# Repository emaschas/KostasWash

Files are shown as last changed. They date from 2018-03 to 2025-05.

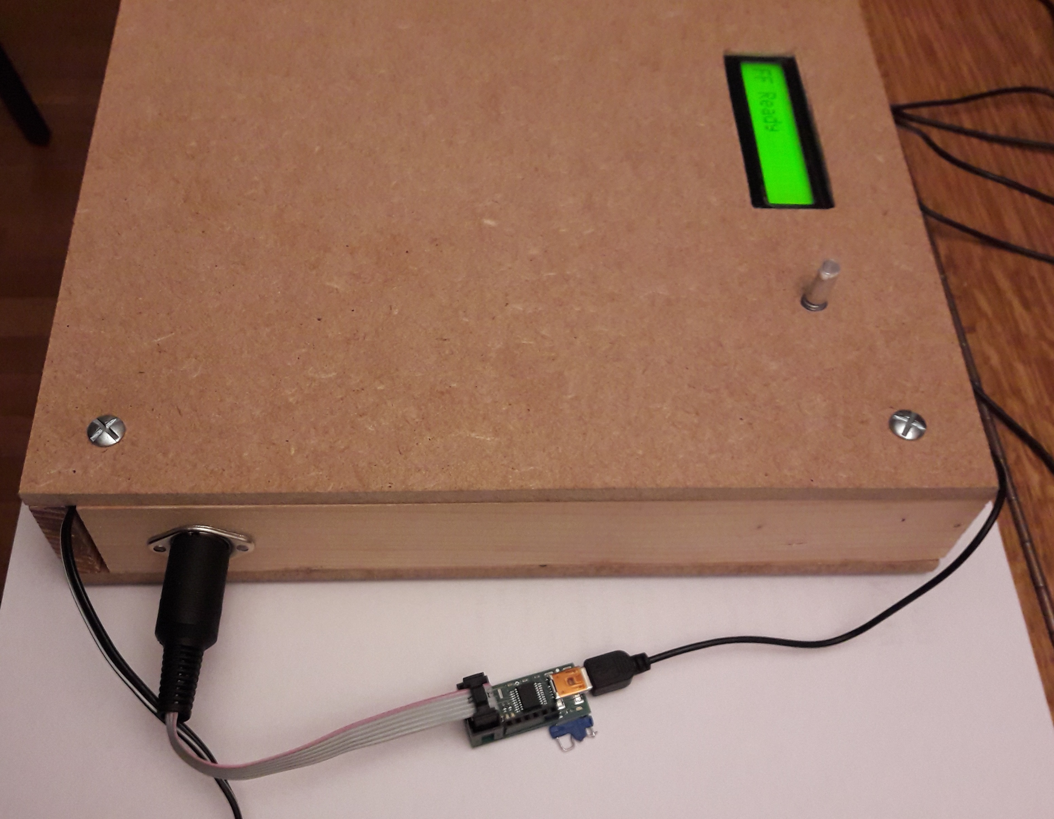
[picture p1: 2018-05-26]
Hardware/Controller_02.jpg

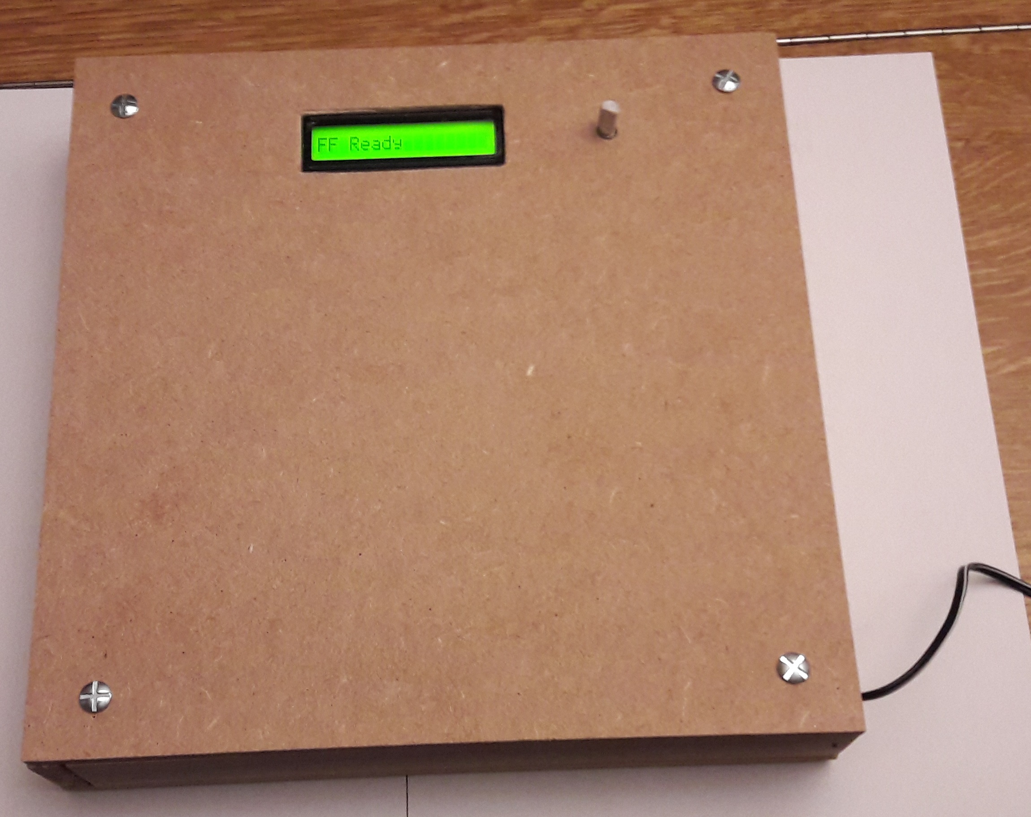
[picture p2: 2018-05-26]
Hardware/Controller_01.jpg

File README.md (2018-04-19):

# KostasWash
<h1>AVR based Washing machine controller</h1>
<h2>Object</h2>
This software is a washing machine controller based on an ATMEGA8535.
<h2>Human interface</h2>
The human interface is based on a LCD and a rotary encoder.
<h2>Power interface</h2>
The power interface is based on a 16 relay board.
<h2>Mechanical part</h2>
The washing machine is an old GROENJE WA583 with a broken mechanical programmer.<br>
The diagram and some other information can be found in the "Documentation" folder.
<h2>More details</h2>
See the <i>Wiki</i> pages for more details...

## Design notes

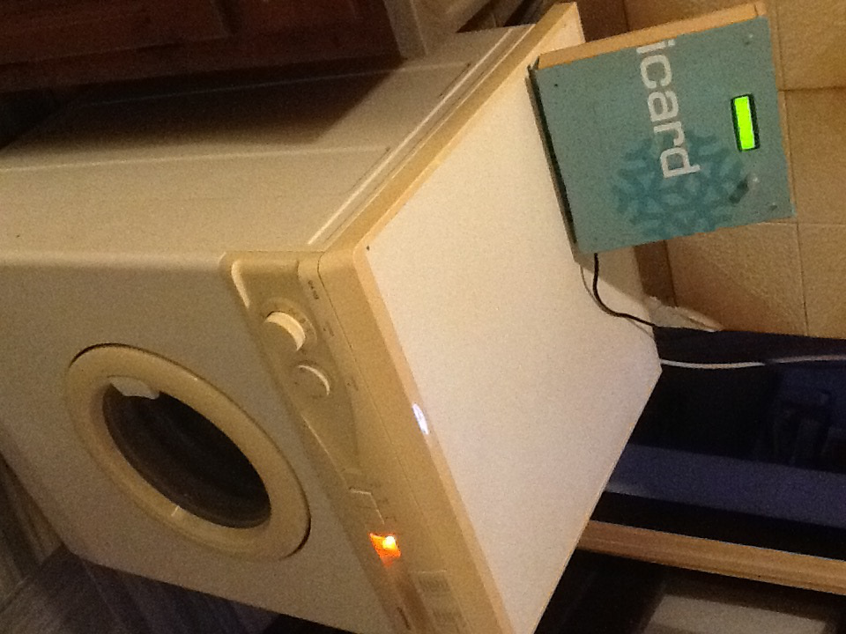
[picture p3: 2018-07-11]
Hardware/General_View.jpeg

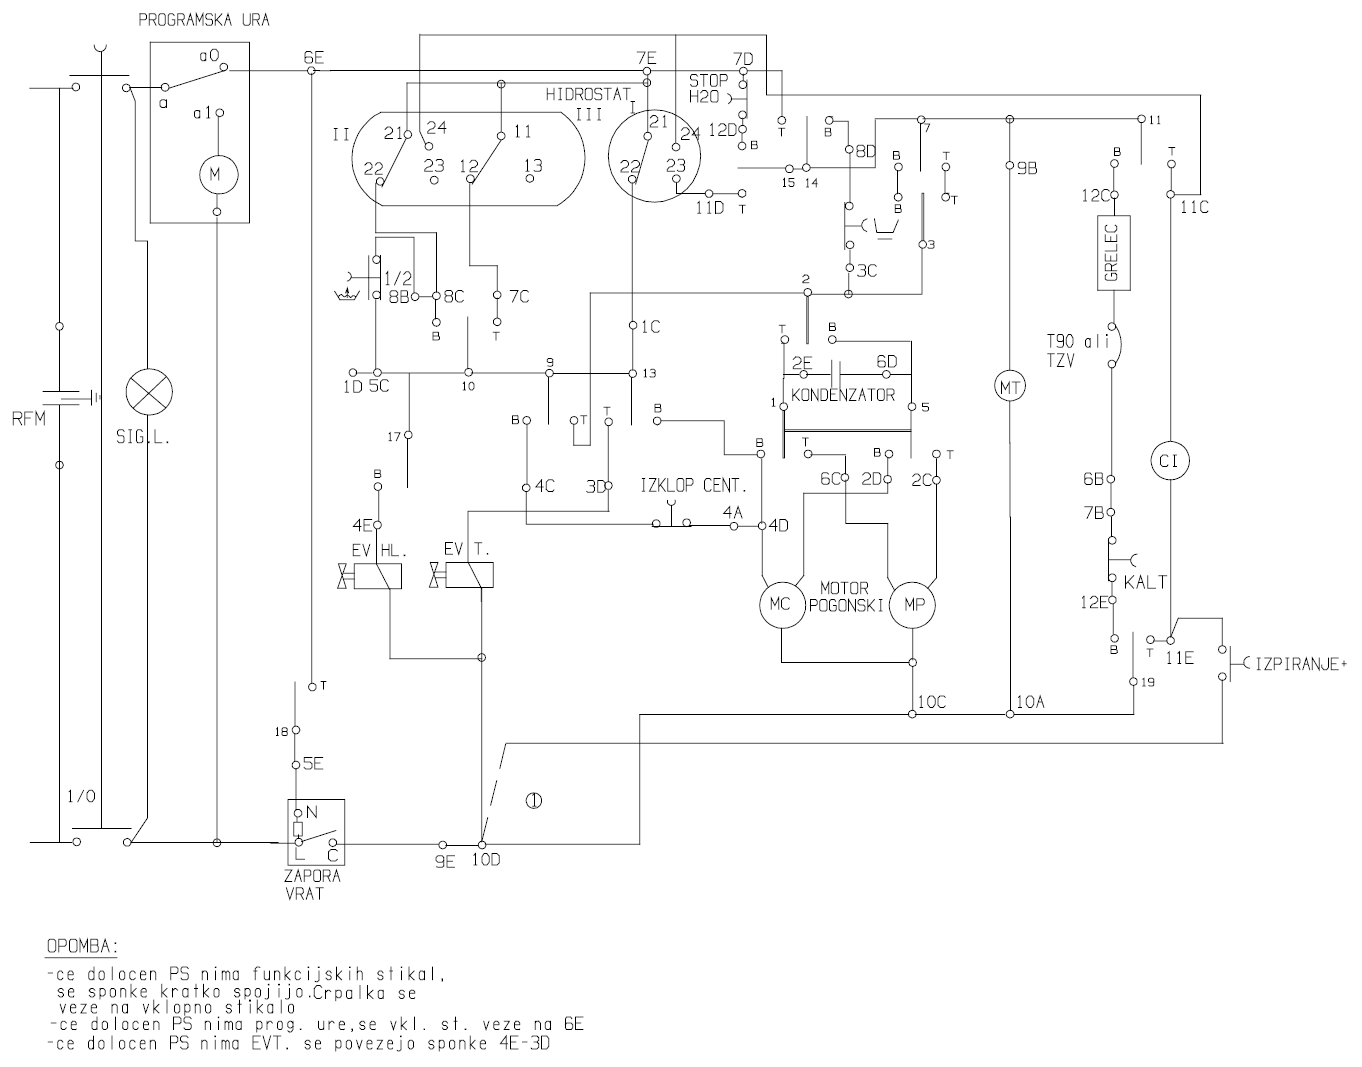
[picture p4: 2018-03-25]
Documentation/WA583 Diagram.png

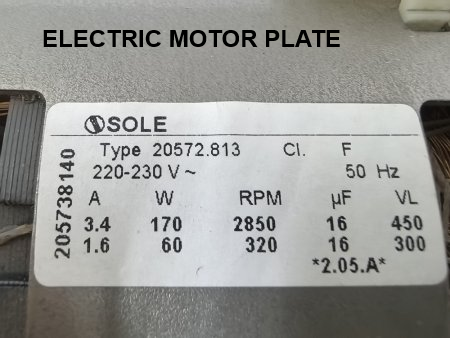
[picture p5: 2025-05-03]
Documentation/Gorenje WA583 Motor 606278.png

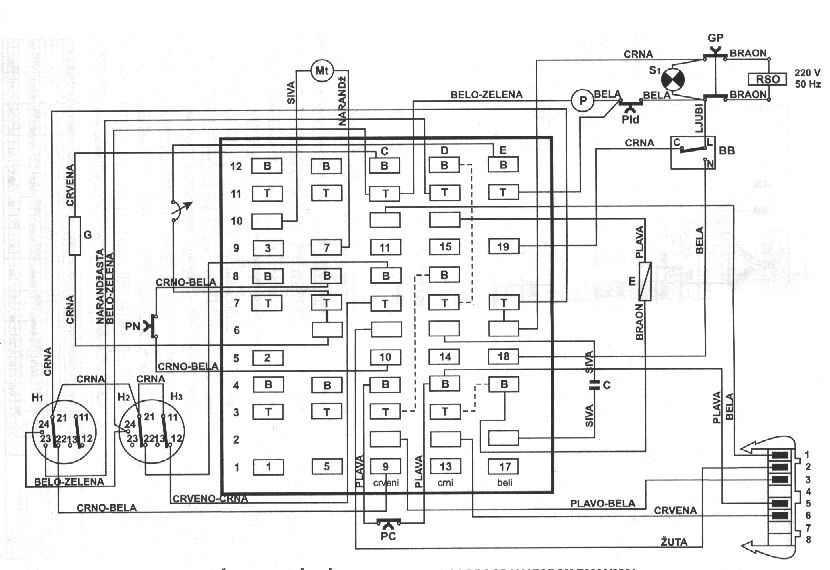
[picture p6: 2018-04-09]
Documentation/wa583 PCB.jpg

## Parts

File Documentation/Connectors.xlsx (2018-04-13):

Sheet: Initial
 | CONNECTEUR C - Rouge |  |  | CONNECTEUR D - Noir |  |  | CONNECTEUR E - Blanc
C1 | Pressure Switch B - 22 (L1) | Black/White | D1 | N.C. | - | E1 | N.C. | -
C2 | Wash Motor 1 | Blue/White | D2 | Spin Motor 1 | Red | E2 | Capacitor | Gray
C3 | Switch 2 | Yellow | D3 | Hot Water Valve | Brown | E3 | N.C. | -
C4 | Switch 2 | Blue/White | D4 | Spin Motor 2 | Blue | E4 | Cold Water Valve | Brown
C5 | Switch 3 | Black/White | D5 | N.C. | - | E5 | Door Lock - N | White
C6 | Wash Motor 2 | Yellow | D6 | Capacitor | Gray | E6 | Switch 1 - Power | Black
C7 | Pressure Switch A - 12 (L3) | Black/Red | D7 | "Stop" Switch | ? | E7 | Pressure Switch Common | Black
C8 | Pressure Switch A - 22 (L2) | ? | D8 | Switch 2 | Yellow | E8 | N.C. | -
C9 | N.C. | - | D9 | N.C. | - | E9 | Door Lock - C | Black
C10 | Wash and Spin Motors Common | Blanc | D10 | Valves Common | Blue | E10 | N.C. | -
C11 | Pressure Switch HH + Drain Pump | Green/White Green/White | D11 | Pressure Switch B - 23 (H1) | Orange | E11 | Drain Pump + Switch S4 | White
C12 | Heater | Red | D12 | "Stop" Switch | ? | E12 | Thermostat | ?

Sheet: Final
 | CONNECTEUR C - Rouge |  |  | CONNECTEUR D - Noir |  |  | CONNECTEUR E - Blanc
C1 | Pressure Switch B - 22 (L1) | Black/White | D1 | N.C. | - | E1 | N.C. | -
C2 | Wash Motor 1 | Blue/White | D2 | Spin Motor 1 | Red | E2 | Capacitor | Gray
C3 | N.C. | - | D3 | Hot Water Valve | Brown | E3 | N.C. | -
C4 | N.C. | - | D4 | Spin Motor 2 | Blue | E4 | Cold Water Valve | Brown
C5 | N.C. | - | D5 | N.C. | - | E5 | Door Lock - N | White
C6 | Wash Motor 2 | Yellow | D6 | Capacitor | Gray | E6 | Switch 1 - Power | Black
C7 | Pressure Switch A - 12 (L3) | Black/Red | D7 | N.C. | N.C. | E7 | Pressure Switch Common | Black
C8 | Pressure Switch A - 22 (L2) | ? | D8 | N.C. | N.C. | E8 | N.C. | -
C9 | N.C. | - | D9 | N.C. | - | E9 | Door Lock - C | Black
C10 | Wash and Spin Motors Common | Blanc | D10 | Valves Common | Blue | E10 | N.C. | -
C11 | Pressure Switch HH + Drain Pump | Green/White Green/White | D11 | Pressure Switch B - 23 (H1) | Orange | E11 | Drain Pump | White
C12 | Heater | Red | D12 | N.C. | - | E12 | Thermostat | ?

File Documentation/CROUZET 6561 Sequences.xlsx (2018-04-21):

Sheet: Chart
ID | PROGRAM | CONTACT |  | NORMAL |  |  |  |  |  |  |  |  |  |  |  |  |  |  |  |  |  |  |  |  |  |  |  |  |  |  |  |  | DELICATES |  |  |  |  |  |  |  |  |  |  |  |  |  |  |  |  |  |  | WOOL
 | CROUZET 6561 | ID | POS | A |  |  |  | B |  |  | C |  | D |  |  |  |  |  | E |  |  |  |  |  |  |  |  | F |  |  |  | STOP | G |  |  |  | H |  | J |  |  |  | K |  |  |  |  | L |  |  | STOP | M
 |  |  |  | 1 | 2 | 3 | 4 | 5 | 6 | 7 | 8 | 9 | 10 | 11 | 12 | 13 | 14 | 15 | 16 | 17 | 18 | 19 | 20 | 21 | 22 | 23 | 24 | 25 | 26 | 27 | 28 | 29 | 1 | 2 | 3 | 4 | 5 | 6 | 7 | 8 | 9 | 10 | 11 | 12 | 13 | 14 | 15 | 16 | 17 | 18 | 19 | 1 | 2 | 3 | 4 | 5 | 6 | 7 | 8
19 | PUMP | 19 | T | x |  | x | x | x |  |  | x |  | x |  |  | x | x | x | x | x | x | x |  |  | x | x | x | x | x | x | x | x | x |  | x | x | x |  | x |  |  | x | x | x | x | x | x | x | x | x | x | x |  | x | x | x | x | x | x
 | HEATER |  | B |  | x |  |  |  | x | x |  | x |  | x | x |  |  |  |  |  |  |  |  |  |  |  |  |  |  |  |  |  |  | x |  |  |  | x |  | x | x |  |  |  |  |  |  |  |  |  |  |  | x
18 | DOOR LOCK | 18 | T | x | x | x | x | x | x | x | x | x | x | x | x | x | x | x | x | x | x | x | x | x | x | x | x | x | x | x | x |  | x | x | x | x | x | x | x | x | x | x | x | x | x | x | x | x | x | x |  | x | x | x | x | x | x | x | x
 | - |  | B
17 | - | 17 | T
 | COLD WATER VALVE |  | B | x | x | x |  |  |  |  | x | x | x | x | x | x | x |  | x |  |  | x |  |  | x |  |  | x |  |  |  |  | x | x | x |  |  |  |  |  |  |  | x |  |  | x |  | x |  |  |  | x | x | x |  | x |  | x
15 | PROGRAMMER ON HB23 | 15 | T | x | x | x | x | x | x | x | x | x | x | x | x | x | x | x | x | x | x | x | x | x | x | x | x | x |  |  |  |  |  |  |  | x | x | x | x | x | x | x | x | x | x | x | x |  |  |  | x | x | x | x | x | x | x | x | x
 | STOP PUMP |  | B |  |  |  |  |  |  |  |  |  |  |  |  |  |  |  |  |  |  |  |  |  |  |  |  |  | x | x | x |  |  |  |  |  |  |  |  |  |  |  |  |  |  |  |  |  | x | x
14 | PROGRAMMER DIRECT | 14 | T |  |  |  | x |  |  |  |  |  |  |  |  |  |  | x |  | x | x |  | x | x |  | x | x |  |  | x | x |  |  |  |  | x |  |  |  |  |  | x |  | x | x |  | x |  |  | x |  |  |  |  | x |  | x |  | x
 | WASHING 10"/5" |  | B |  |  | x |  |  |  |  |  |  |  | x |  | x |  |  | x |  |  | x |  |  | x |  |  | x |  |  |  |  |  |  |  |  |  |  |  |  | x
13 | HOT WATER VALVE | 13 | T |  |  |  |  | x | x | x | x | x |  |  |  |  |  |  |  |  |  |  |  |  |  |  |  |  |  |  |  |  |  |  |  |  | x | x
 | SPINNING |  | B |  |  |  |  |  |  |  |  |  |  |  |  |  |  |  |  |  |  |  |  |  |  |  |  |  |  | x
11 | PUMP | 11 | T |  |  |  | x |  |  |  |  |  |  |  |  |  |  | x |  | x | x |  | x | x |  | x | x |  | x | x | x |  |  |  |  | x |  |  |  |  |  | x |  | x | x |  | x |  | x | x |  |  |  |  | x |  | x |  | x
 | HEATER |  | B |  | x |  |  |  | x | x |  | x |  | x |  |  |  |  |  |  |  |  |  |  |  |  |  |  |  |  |  |  |  | x |  |  |  | x |  | x | x |  |  |  |  |  |  |  |  |  |  |  | x
10 | LEVEL III | 10 | T |  |  |  |  |  |  |  |  |  |  |  |  |  |  |  |  |  |  |  |  |  |  |  |  |  |  |  |  | x |  |  |  |  |  |  |  |  |  |  | x |  |  | x |  | x |  |  | x | x | x | x |  | x |  | x
 | LEVEL III |  | B | x | x | x |  |  |  |  |  |  |  |  |  |  |  |  | x |  |  | x |  |  | x |  |  | x |  |  |  |  | x | x | x |  | x | x | x | x | x
9 | COOLING | 9 | T |  |  |  |  |  |  |  |  |  |  |  |  |  | x
 | SKIP SPINNING |  | B |  |  |  |  |  |  |  |  |  |  |  |  |  |  |  |  |  | x |  |  | x |  |  | x |  |  |  | x |  |  |  |  |  |  |  |  |  |  |  |  |  | x |  |  |  |  | x
7 | WASHING 4"/11" | 7 | T | x | x | x |  | x | x | x | x | x | x | x | x | x | x |  | x | x |  | x | x |  | x | x |  | x | x |  |  |  | x | x | x |  | x | x | x | x | x |  | x | x |  | x |  | x | x
 | WASHING 4"/26" |  | B |  |  |  |  |  |  |  |  |  |  |  |  |  |  |  |  |  |  |  |  |  |  |  |  |  |  |  |  |  |  |  |  |  |  |  |  |  |  |  |  |  |  |  |  |  |  |  |  | x |  | x |  | x |  | x
5/1 | WASHING | 5/1 | T | x | x | x |  | x | x | x | x | x | x | x | x | x | x |  | x | x |  | x | x |  | x | x |  | x | x |  |  | x | x | x | x |  | x | x | x | x | x |  | x | x |  | x |  | x | x |  | x | x |  | x |  | x |  | x
 | SPINNING |  | B |  |  |  |  |  |  |  |  |  |  |  |  |  |  |  |  |  | x |  |  | x |  |  | x |  |  | x | x |  |  |  |  |  |  |  |  |  |  |  |  |  | x |  |  |  |  | x
 |  |  |  | 240"
3 | MIXING 4"/11" | 3 | T | x |  |  | o |  |  |  | x |  |  |  |  | o |  |  | x |  |  | o |  |  |  | x |  |  |  |  | o |  |  | x |  |  | o |  |  |  | x |  |  |  |  | o |  |  | x |  |  | o |  |  |  | x
 | MIXING 4"/26" |  | B |  |  |  |  | o |  |  |  | x |  |  |  |  |  |  |  |  |  |  | o |  |  |  | x |  |  |  |  |  |  |  |  |  |  | o |  |  |  | x |  |  |  |  |  |  |  |  |  |  | o |  |  |  | x
2 | MIXING 10"/5" | 2 | T |  |  | o | o | o |  |  |  |  |  | o | o | o |  |  |  |  | o | o | o |  |  |  |  |  | o | o | o |  |  |  |  | o | o | o |  |  |  |  |  | o | o | o |  |  |  |  |  | o | o | o
 |  |  | B | x |  |  |  |  |  | x | x | x |  |  |  |  | x | x | x |  |  |  |  |  | x | x | x |  |  |  |  | x | x | x |  |  |  |  |  | x | x | x |  |  |  |  |  | x | x | x |  |  |  |  |  | x | x | x

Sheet: Simulateur
 | WA583 SIMALTOR
 | POS | STEP | 19T | 19B | 18T | 18B | 17T | 17B | 15T | 15B | 14T | 14B | 13T | 13B | 11T | 11B | 10T | 10B | 9T | 9B | 7T | 7B | 5T | 5B | 1T | 1B | STEP | BUS1 | BUS2 | BUS3 | DOOR LOCK | MT PROG | MP WASH | MC SPIN | HEAT | PUMP | COLD VALVE | HOT VALVE
NORMAL | A | 1 | x |  | x |  |  | x | x |  |  |  |  |  |  |  |  | x |  |  | x |  | x |  | x |  | 1 | H1 | L2 | R4/11 | ON | H1 | R4/11 |  |  |  | L2
 |  | 2 |  | x | x |  |  | x | x |  |  |  |  |  |  | x |  | x |  |  | x |  | x |  | x |  | 2 | H1 | L2 | R4/11 | ON | H1 | R4/11 |  | H1 |  | L2
 |  | 3 | x |  | x |  |  | x | x |  |  | x |  |  |  |  |  | x |  |  | x |  | x |  | x |  | 3 | H1 | L2 | R5/5:S2-R4/11 | ON | H1 | R5/5:S2-R4/11 |  |  |  | L2
 |  | 4 | x |  | x |  |  |  | x |  | x |  |  |  | x |  |  |  |  |  |  |  |  |  |  |  | 4 | ON | L1 |  | ON | ON |  |  |  | ON
 | B | 5 | x |  | x |  |  |  | x |  |  |  | x |  |  |  |  |  |  |  | x |  | x |  | x |  | 5 | H1 | L1 | R4/11 | ON | H1 | R4/11 |  |  |  |  | L1
 |  | 6 |  | x | x |  |  |  | x |  |  |  | x |  |  | x |  |  |  |  | x |  | x |  | x |  | 6 | H1 | L1 | R4/11 | ON | H1 | R4/11 |  | H1 |  |  | L1
 |  | 7 |  | x | x |  |  |  | x |  |  |  | x |  |  | x |  |  |  |  | x |  | x |  | x |  | 7 | H1 | L1 | R4/11 | ON | H1 | R4/11 |  | H1 |  |  | L1
 | C | 8 | x |  | x |  |  | x | x |  |  |  | x |  |  |  |  |  |  |  | x |  | x |  | x |  | 8 | H1 | L1 | R4/11 | ON | H1 | R4/11 |  |  |  | L1 | L1
 |  | 9 |  | x | x |  |  | x | x |  |  |  | x |  |  | x |  |  |  |  | x |  | x |  | x |  | 9 | H1 | L1 | R4/11 | ON | H1 | R4/11 |  | H1 |  | L1 | L1
 | D | 10 | x |  | x |  |  | x | x |  |  |  |  |  |  |  |  |  |  |  | x |  | x |  | x |  | 10 | H1 | L1 | R4/11 | ON | H1 | R4/11 |  |  |  | L1
 |  | 11 |  | x | x |  |  | x | x |  |  | x |  |  |  | x |  |  |  |  | x |  | x |  | x |  | 11 | H1 | L1 | R5/5:S2-R4/11 | ON | H1 | R5/5:S2-R4/11 |  | H1 |  | L1
 |  | 12 |  | x | x |  |  | x | x |  |  |  |  |  |  |  |  |  |  |  | x |  | x |  | x |  | 12 | H1 | L1 | R4/11 | ON | H1 | R4/11 |  |  |  | L1
 |  | 13 | x |  | x |  |  | x | x |  |  | x |  |  |  |  |  |  |  |  | x |  | x |  | x |  | 13 | H1 | L1 | R5/5:S2-R4/11 | ON | H1 | R5/5:S2-R4/11 |  |  |  | L1
 |  | 14 | x |  | x |  |  | x | x |  |  |  |  |  |  |  |  |  | x |  | x |  | x |  | x |  | 14 | H1 | L1 | L1R4/11 | ON | H1 | L1R4/11 |  |  |  | L1
 |  | 15 | x |  | x |  |  |  | x |  | x |  |  |  | x |  |  |  |  |  |  |  |  |  |  |  | 15 | ON | L1 |  | ON | ON |  |  |  | ON
 | E | 16 | x |  | x |  |  | x | x |  |  | x |  |  |  |  |  | x |  |  | x |  | x |  | x |  | 16 | H1 | L2 | R5/5:S2-R4/11 | ON | H1 | R5/5:S2-R4/11 |  |  |  | L2
 |  | 17 | x |  | x |  |  |  | x |  | x |  |  |  | x |  |  |  |  |  | x |  | x |  | x |  | 17 | ON | L1 | R4/11 | ON | ON | R4/11 |  |  | ON
 |  | 18 | x |  | x |  |  |  | x |  | x |  |  |  | x |  |  |  |  | x |  |  |  | x |  | x | 18 | ON | L1 |  | ON | ON |  | L1+S2 |  | ON
 |  | 19 | x |  | x |  |  | x | x |  |  | x |  |  |  |  |  | x |  |  | x |  | x |  | x |  | 19 | H1 | L2 | R5/5:S2-R4/11 | ON | H1 | R5/5:S2-R4/11 |  |  |  | L2
 |  | 20 |  |  | x |  |  |  | x |  | x |  |  |  | x |  |  |  |  |  | x |  | x |  | x |  | 20 | ON | L1 | R4/11 | ON | ON | R4/11
 |  | 21 |  |  | x |  |  |  | x |  | x |  |  |  | x |  |  |  |  | x |  |  |  | x |  | x | 21 | ON | L1 |  | ON | ON |  | L1+S2
 |  | 22 | x |  | x |  |  | x | x |  |  | x |  |  |  |  |  | x |  |  | x |  | x |  | x |  | 22 | H1 | L2 | R5/5:S2-R4/11 | ON | H1 | R5/5:S2-R4/11 |  |  |  | L2
 |  | 23 | x |  | x |  |  |  | x |  | x |  |  |  | x |  |  |  |  |  | x |  | x |  | x |  | 23 | ON | L1 | R4/11 | ON | ON | R4/11 |  |  | ON
 |  | 24 | x |  | x |  |  |  | x |  | x |  |  |  | x |  |  |  |  | x |  |  |  | x |  | x | 24 | ON | L1 |  | ON | ON |  | L1+S2 |  | ON
 | F | 25 | x |  | x |  |  | x | x |  |  | x |  |  |  |  |  | x |  |  | x |  | x |  | x |  | 25 | H1 | L2 | R5/5:S2-R4/11 | ON | H1 | R5/5:S2-R4/11 |  |  |  | L2
 |  | 26 | x |  | x |  |  |  |  | x |  |  |  |  | x |  |  |  |  |  | x |  | x |  | x |  | 26 | STOP | L1 | R4/11 | ON | STOP | R4/11 |  |  | STOP
 |  | 27 | x |  | x |  |  |  |  | x | x |  |  | x | x |  |  |  |  |  |  |  |  | x |  | x | 27 | ON | L1 |  | ON | ON |  | L1 |  | ON
 |  | 28 | x |  | x |  |  |  |  | x | x |  |  |  | x |  |  |  |  | x |  |  |  | x |  | x | 28 | ON | L1 |  | ON | ON |  | L1+S2 |  | ON
 | STOP | 29 | x |  |  |  |  |  |  |  |  |  |  |  |  |  | x |  |  |  |  |  | x |  | x |  | 29 |  | L3
DELICATES | G | 1 | x |  | x |  |  | x |  |  |  |  |  |  |  |  |  | x |  |  | x |  | x |  | x |  | 1 |  | L2 | R4/11 | ON |  | R4/11 |  |  |  | L2
 |  | 2 |  | x | x |  |  | x |  |  |  |  |  |  |  | x |  | x |  |  | x |  | x |  | x |  | 2 |  | L2 | R4/11 | ON |  | R4/11 |  |  |  | L2
 |  | 3 | x |  | x |  |  | x |  |  |  |  |  |  |  |  |  | x |  |  | x |  | x |  | x |  | 3 |  | L2 | R4/11 | ON |  | R4/11 |  |  |  | L2
 |  | 4 | x |  | x |  |  |  | x |  | x |  |  |  | x |  |  |  |  |  |  |  |  |  |  |  | 4 | ON | L1 |  | ON | ON |  |  |  | ON
 | H | 5 | x |  | x |  |  |  | x |  |  |  | x |  |  |  |  | x |  |  | x |  | x |  | x |  | 5 | H1 | L2 | R4/11 | ON | H1 | R4/11 |  |  |  |  | L2
 |  | 6 |  | x | x |  |  |  | x |  |  |  | x |  |  | x |  | x |  |  | x |  | x |  | x |  | 6 | H1 | L2 | R4/11 | ON | H1 | R4/11 |  | H1 |  |  | L2
 | J | 7 | x |  | x |  |  |  | x |  |  |  |  |  |  |  |  | x |  |  | x |  | x |  | x |  | 7 | H1 | L2 | R4/11 | ON | H1 | R4/11
 |  | 8 |  | x | x |  |  |  | x |  |  |  |  |  |  | x |  | x |  |  | x |  | x |  | x |  | 8 | H1 | L2 | R4/11 | ON | H1 | R4/11 |  | H1
 |  | 9 |  | x | x |  |  |  | x |  |  | x |  |  |  | x |  | x |  |  | x |  | x |  | x |  | 9 | H1 | L2 | R5/5:S2-R4/11 | ON | H1 | R5/5:S2-R4/11 |  | H1
 |  | 10 | x |  | x |  |  |  | x |  | x |  |  |  | x |  |  |  |  |  |  |  |  |  |  |  | 10 | ON | L1 |  | ON | ON |  |  |  | ON
 | K | 11 | x |  | x |  |  | x | x |  |  |  |  |  |  |  | x |  |  |  | x |  | x |  | x |  | 11 | H1 | L3 | R4/11 | ON | H1 | R4/11 |  |  |  | L3
 |  | 12 | x |  | x |  |  |  | x |  | x |  |  |  | x |  |  |  |  |  | x |  | x |  | x |  | 12 | ON | L1 | R4/11 | ON | ON | R4/11 |  |  | ON
 |  | 13 | x |  | x |  |  |  | x |  | x |  |  |  | x |  |  |  |  | x |  |  |  | x |  | x | 13 | ON | L1 |  | ON | ON |  | L1+S2 |  | ON
 |  | 14 | x |  | x |  |  | x | x |  |  |  |  |  |  |  | x |  |  |  | x |  | x |  | x |  | 14 | H1 | L3 | R4/11 | ON | H1 | R4/11 |  |  |  | L3
 |  | 15 | x |  | x |  |  |  | x |  | x |  |  |  | x |  |  |  |  |  |  |  |  |  |  |  | 15 | ON | L1 |  | ON | ON |  |  |  | ON
 | L | 16 | x |  | x |  |  | x |  |  |  |  |  |  |  |  | x |  |  |  | x |  | x |  | x |  | 16 |  | L3 | R4/11 | ON |  | R4/11 |  |  |  | L3
 |  | 17 | x |  | x |  |  |  |  | x |  |  |  |  | x |  |  |  |  |  | x |  | x |  | x |  | 17 | STOP | L1 | R4/11 | ON | STOP | R4/11 |  |  | STOP
 |  | 18 | x |  | x |  |  |  |  | x | x |  |  |  | x |  |  |  |  | x |  |  |  | x |  | x | 18 | ON | L1 |  | ON | ON |  | L1+S2 |  | ON
 | STOP | 19 | x |  |  |  |  |  | x |  |  |  |  |  |  |  | x |  |  |  |  |  | x |  | x |  | 19 | H1 | L3
WOOL | M | 1 | x |  | x |  |  | x | x |  |  |  |  |  |  |  | x |  |  |  |  | x | x |  | x |  | 1 | H1 | L3 | R4/26 | ON | H1 | R4/26 |  |  |  | L3
 |  | 2 |  | x | x |  |  | x | x |  |  |  |  |  |  | x | x |  |  |  |  |  |  |  |  |  | 2 | H1 | L3 |  | ON | H1 |  |  | H1 |  | L3
 |  | 3 | x |  | x |  |  | x | x |  |  |  |  |  |  |  | x |  |  |  |  | x | x |  | x |  | 3 | H1 | L3 | R4/26 | ON | H1 | R4/26 |  |  |  | L3
 |  | 4 | x |  | x |  |  |  | x |  | x |  |  |  | x |  |  |  |  |  |  |  |  |  |  |  | 4 | ON | L1 |  | ON | ON |  |  |  | ON
 |  | 5 | x |  | x |  |  | x | x |  |  |  |  |  |  |  | x |  |  |  |  | x | x |  | x |  | 5 | H1 | L3 | R4/26 | ON | H1 | R4/26 |  |  |  | L3
 |  | 6 | x |  | x |  |  |  | x |  | x |  |  |  | x |  |  |  |  |  |  |  |  |  |  |  | 6 | ON | L1 |  | ON | ON |  |  |  | ON
 |  | 7 | x |  | x |  |  | x | x |  |  |  |  |  |  |  | x |  |  |  |  | x | x |  | x |  | 7 | H1 | L3 | R4/26 | ON | H1 | R4/26 |  |  |  | L3
 |  | 8 | x |  | x |  |  |  | x |  | x |  |  |  | x |  |  |  |  |  |  |  |  |  |  |  | 8 | ON | L1 |  | ON | ON |  |  |  | ON
 |  | 9 | x |  | x |  |  | x | x |  |  |  |  |  |  |  | x |  |  |  |  | x | x |  | x |  | 9 | H1 | L3 | R4/26 | ON | H1 | R4/26 |  |  |  | L3
 |  | 10 | x |  | x |  |  |  | x |  | x |  |  |  | x |  |  |  |  |  | x |  | x |  | x |  | 10 | ON | L1 | R4/11 | ON | ON | R4/11 |  |  | ON
 |  | 11 | x |  | x |  |  |  | x |  | x |  |  |  | x |  |  |  |  | x |  |  |  | x |  | x | 11 | ON | L1 |  | ON | ON |  | L1+S2 |  | ON
 | STOP | 12 | x |  |  |  |  |  | x |  |  |  |  |  |  |  | x |  |  |  |  |  | x |  | x |  | 12 | H1 | L3

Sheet: Simulateur (corrigé)
 | WA583 SIMALTOR
 | POS | STEP | 19T | 19B | 18T | 18B | 17T | 17B | 15T | 15B | 14T | 14B | 13T | 13B | 11T | 11B | 10T | 10B | 9T | 9B | 7T | 7B | 5T | 5B | 1T | 1B | STEP | BUS1 | BUS2 | BUS3 | DOOR LOCK | MT PROG | MP WASH | MC SPIN | HEAT | PUMP | COLD VALVE | HOT VALVE
NORMAL | A | 1 | x |  | x |  |  | x | x |  |  |  |  |  |  |  |  | x |  |  | x |  | x |  | x |  | 1 | H1 | L2 | R4/11 | ON | H1 | R4/11 |  |  |  | L2
 |  | 2 |  | x | x |  |  | x | x |  |  |  |  |  |  | x |  | x |  |  | x |  | x |  | x |  | 2 | H1 | L2 | R4/11 | ON | H1 | R4/11 |  | H1 |  | L2
 |  | 3 | x |  | x |  |  | x | x |  |  | x |  |  |  |  |  | x |  |  | x |  | x |  | x |  | 3 | H1 | L2 | R5/5:S2-R4/11 | ON | H1 | R5/5:S2-R4/11 |  |  |  | L2
 |  | 4 | x |  | x |  |  |  | x |  | x |  |  |  | x |  |  |  |  |  |  |  |  |  |  |  | 4 | ON | L1 |  | ON | ON |  |  |  | ON
 | B | 5 | x |  | x |  |  | o | x |  |  |  | x |  |  |  |  |  |  |  | x |  | x |  | x |  | 5 | H1 | L1 | R4/11 | ON | H1 | R4/11 |  |  |  | L1 | L1
 |  | 6 |  | x | x |  |  | o | x |  |  |  | x |  |  | x |  |  |  |  | x |  | x |  | x |  | 6 | H1 | L1 | R4/11 | ON | H1 | R4/11 |  | H1 |  | L1 | L1
 |  | 7 |  | x | x |  |  | o | x |  |  |  | x |  |  | x |  |  |  |  | x |  | x |  | x |  | 7 | H1 | L1 | R4/11 | ON | H1 | R4/11 |  | H1 |  | L1 | L1
 | C | 8 | x |  | x |  |  | x | x |  |  |  | x |  |  |  |  |  |  |  | x |  | x |  | x |  | 8 | H1 | L1 | R4/11 | ON | H1 | R4/11 |  |  |  | L1 | L1
 |  | 9 |  | x | x |  |  | x | x |  |  |  | x |  |  | x |  |  |  |  | x |  | x |  | x |  | 9 | H1 | L1 | R4/11 | ON | H1 | R4/11 |  | H1 |  | L1 | L1
 | D | 10 | x |  | x |  |  | x | x |  |  |  |  |  |  |  |  |  |  |  | x |  | x |  | x |  | 10 | H1 | L1 | R4/11 | ON | H1 | R4/11 |  |  |  | L1
 |  | 11 |  | x | x |  |  | x | x |  |  | x |  |  |  | x |  |  |  |  | x |  | x |  | x |  | 11 | H1 | L1 | R5/5:S2-R4/11 | ON | H1 | R5/5:S2-R4/11 |  | H1 |  | L1
 |  | 12 |  | x | x |  |  | x | x |  |  |  |  |  |  |  |  |  |  |  | x |  | x |  | x |  | 12 | H1 | L1 | R4/11 | ON | H1 | R4/11 |  |  |  | L1
 |  | 13 | x |  | x |  |  | x | x |  |  | x |  |  |  |  |  |  |  |  | x |  | x |  | x |  | 13 | H1 | L1 | R5/5:S2-R4/11 | ON | H1 | R5/5:S2-R4/11 |  |  |  | L1
 |  | 14 | x |  | x |  |  | x | x |  |  |  |  |  |  |  |  |  |  |  | x |  | x |  | x |  | 14 | H1 | L1 | R4/11 | ON | H1 | R4/11 |  |  |  | L1
 |  | 15 | x |  | x |  |  |  | x |  | x |  |  |  | x |  |  |  |  |  |  |  |  |  |  |  | 15 | ON | L1 |  | ON | ON |  |  |  | ON
 | E | 16 | x |  | x |  |  | x | x |  |  | x |  |  |  |  |  | x |  |  | x |  | x |  | x |  | 16 | H1 | L2 | R5/5:S2-R4/11 | ON | H1 | R5/5:S2-R4/11 |  |  |  | L2
 |  | 17 | x |  | x |  |  |  | x |  | x |  |  |  | x |  |  |  |  |  | x |  | x |  | x |  | 17 | ON | L1 | R4/11 | ON | ON | R4/11 |  |  | ON
 |  | 18 | x |  | x |  |  |  | x |  | x |  |  |  | x |  |  |  |  | x |  |  |  | x |  | x | 18 | ON | L1 |  | ON | ON |  | L1+S2 |  | ON
 |  | 19 | x |  | x |  |  | x | x |  |  | x |  |  |  |  |  | x |  |  | x |  | x |  | x |  | 19 | H1 | L2 | R5/5:S2-R4/11 | ON | H1 | R5/5:S2-R4/11 |  |  |  | L2
 |  | 20 | o |  | x |  |  |  | x |  | x |  |  |  | x |  |  |  |  |  | x |  | x |  | x |  | 20 | ON | L1 | R4/11 | ON | ON | R4/11 |  |  | ON
 |  | 21 | o |  | x |  |  |  | x |  | x |  |  |  | x |  |  |  |  | x |  |  |  | x |  | x | 21 | ON | L1 |  | ON | ON |  | L1+S2 |  | ON
 |  | 22 | x |  | x |  |  | x | x |  |  | x |  |  |  |  |  | x |  |  | x |  | x |  | x |  | 22 | H1 | L2 | R5/5:S2-R4/11 | ON | H1 | R5/5:S2-R4/11 |  |  |  | L2
 |  | 23 | x |  | x |  |  |  | x |  | x |  |  |  | x |  |  |  |  |  | x |  | x |  | x |  | 23 | ON | L1 | R4/11 | ON | ON | R4/11 |  |  | ON
 |  | 24 | x |  | x |  |  |  | x |  | x |  |  |  | x |  |  |  |  | x |  |  |  | x |  | x | 24 | ON | L1 |  | ON | ON |  | L1+S2 |  | ON
 | F | 25 | x |  | x |  |  | x | x |  |  | x |  |  |  |  |  | x |  |  | x |  | x |  | x |  | 25 | H1 | L2 | R5/5:S2-R4/11 | ON | H1 | R5/5:S2-R4/11 |  |  |  | L2
 |  | 26 | x |  | x |  |  |  |  | x |  |  |  |  | x |  |  |  |  |  | x |  | x |  | x |  | 26 | STOP | L1 | R4/11 | ON | STOP | R4/11 |  |  | STOP
 |  | 27 | x |  | x |  |  |  |  | x | x |  |  | x | x |  |  |  |  |  |  |  |  | x |  | x | 27 | ON | L1 |  | ON | ON |  | L1 |  | ON
 |  | 28 | x |  | x |  |  |  |  | x | x |  |  |  | x |  |  |  |  | x |  |  |  | x |  | x | 28 | ON | L1 |  | ON | ON |  | L1+S2 |  | ON
 | STOP | 29 | x |  |  |  |  |  |  |  |  |  |  |  |  |  | x |  |  |  |  |  | x |  | x |  | 29 |  | L3
DELICATES | G | 1 | x |  | x |  |  | x | o |  |  |  |  |  |  |  |  | x |  |  | x |  | x |  | x |  | 1 | H1 | L2 | R4/11 | ON | H1 | R4/11 |  |  |  | L2
 |  | 2 |  | x | x |  |  | x | o |  |  |  |  |  |  | x |  | x |  |  | x |  | x |  | x |  | 2 | H1 | L2 | R4/11 | ON | H1 | R4/11 |  | H1 |  | L2
 |  | 3 | x |  | x |  |  | x | o |  |  |  |  |  |  |  |  | x |  |  | x |  | x |  | x |  | 3 | H1 | L2 | R4/11 | ON | H1 | R4/11 |  |  |  | L2
 |  | 4 | x |  | x |  |  |  | x |  | x |  |  |  | x |  |  |  |  |  |  |  |  |  |  |  | 4 | ON | L1 |  | ON | ON |  |  |  | ON
 | H | 5 | x |  | x |  |  |  | x |  |  |  | x |  |  |  |  | x |  |  | x |  | x |  | x |  | 5 | H1 | L2 | R4/11 | ON | H1 | R4/11 |  |  |  |  | L2
 |  | 6 |  | x | x |  |  |  | x |  |  |  | x |  |  | x |  | x |  |  | x |  | x |  | x |  | 6 | H1 | L2 | R4/11 | ON | H1 | R4/11 |  | H1 |  |  | L2
 | J | 7 | x |  | x |  |  |  | x |  |  |  |  |  |  |  |  | x |  |  | x |  | x |  | x |  | 7 | H1 | L2 | R4/11 | ON | H1 | R4/11
 |  | 8 |  | x | x |  |  |  | x |  |  |  |  |  |  | x |  | x |  |  | x |  | x |  | x |  | 8 | H1 | L2 | R4/11 | ON | H1 | R4/11 |  | H1
 |  | 9 |  | x | x |  |  |  | x |  |  | x |  |  |  | x |  | x |  |  | x |  | x |  | x |  | 9 | H1 | L2 | R5/5:S2-R4/11 | ON | H1 | R5/5:S2-R4/11 |  | H1
 |  | 10 | x |  | x |  |  |  | x |  | x |  |  |  | x |  |  |  |  |  |  |  |  |  |  |  | 10 | ON | L1 |  | ON | ON |  |  |  | ON
 | K | 11 | x |  | x |  |  | x | x |  |  |  |  |  |  |  | x |  |  |  | x |  | x |  | x |  | 11 | H1 | L3 | R4/11 | ON | H1 | R4/11 |  |  |  | L3
 |  | 12 | x |  | x |  |  |  | x |  | x |  |  |  | x |  |  |  |  |  | x |  | x |  | x |  | 12 | ON | L1 | R4/11 | ON | ON | R4/11 |  |  | ON
 |  | 13 | x |  | x |  |  |  | x |  | x |  |  |  | x |  |  |  |  | x |  |  |  | x |  | x | 13 | ON | L1 |  | ON | ON |  | L1+S2 |  | ON
 |  | 14 | x |  | x |  |  | x | x |  |  |  |  |  |  |  | x |  |  |  | x |  | x |  | x |  | 14 | H1 | L3 | R4/11 | ON | H1 | R4/11 |  |  |  | L3
 |  | 15 | x |  | x |  |  |  | x |  | x |  |  |  | x |  |  |  |  |  |  |  |  |  |  |  | 15 | ON | L1 |  | ON | ON |  |  |  | ON
 | L | 16 | x |  | x |  |  | x | o |  |  |  |  |  |  |  | x |  |  |  | x |  | x |  | x |  | 16 | H1 | L3 | R4/11 | ON | H1 | R4/11 |  |  |  | L3
 |  | 17 | x |  | x |  |  |  |  | x |  |  |  |  | x |  |  |  |  |  | x |  | x |  | x |  | 17 | STOP | L1 | R4/11 | ON | STOP | R4/11 |  |  | STOP
 |  | 18 | x |  | x |  |  |  |  | x | x |  |  |  | x |  |  |  |  | x |  |  |  | x |  | x | 18 | ON | L1 |  | ON | ON |  | L1+S2 |  | ON
 | STOP | 19 | x |  |  |  |  |  | x |  |  |  |  |  |  |  | x |  |  |  |  |  | x |  | x |  | 19 | H1 | L3
WOOL | M | 1 | x |  | x |  |  | x | x |  |  |  |  |  |  |  | x |  |  |  |  | x | x |  | x |  | 1 | H1 | L3 | R4/26 | ON | H1 | R4/26 |  |  |  | L3
 |  | 2 |  | x | x |  |  | x | x |  |  |  |  |  |  | x | x |  |  |  |  |  |  |  |  |  | 2 | H1 | L3 |  | ON | H1 |  |  | H1 |  | L3
 |  | 3 | x |  | x |  |  | x | x |  |  |  |  |  |  |  | x |  |  |  |  | x | x |  | x |  | 3 | H1 | L3 | R4/26 | ON | H1 | R4/26 |  |  |  | L3
 |  | 4 | x |  | x |  |  |  | x |  | x |  |  |  | x |  |  |  |  |  |  |  |  |  |  |  | 4 | ON | L1 |  | ON | ON |  |  |  | ON
 |  | 5 | x |  | x |  |  | x | x |  |  |  |  |  |  |  | x |  |  |  |  | x | x |  | x |  | 5 | H1 | L3 | R4/26 | ON | H1 | R4/26 |  |  |  | L3
 |  | 6 | x |  | x |  |  |  | x |  | x |  |  |  | x |  |  |  |  |  |  |  |  |  |  |  | 6 | ON | L1 |  | ON | ON |  |  |  | ON
 |  | 7 | x |  | x |  |  | x | x |  |  |  |  |  |  |  | x |  |  |  |  | x | x |  | x |  | 7 | H1 | L3 | R4/26 | ON | H1 | R4/26 |  |  |  | L3
 |  | 8 | x |  | x |  |  |  | x |  | x |  |  |  | x |  |  |  |  |  |  |  |  |  |  |  | 8 | ON | L1 |  | ON | ON |  |  |  | ON
 |  | 9 | x |  | x |  |  | x | x |  |  |  |  |  |  |  | x |  |  |  |  | x | x |  | x |  | 9 | H1 | L3 | R4/26 | ON | H1 | R4/26 |  |  |  | L3
 |  | 10 | x |  | x |  |  |  | x |  | x |  |  |  | x |  |  |  |  |  | x |  | x |  | x |  | 10 | ON | L1 | R4/11 | ON | ON | R4/11 |  |  | ON
 |  | 11 | x |  | x |  |  |  | x |  | x |  |  |  | x |  |  |  |  | x |  |  |  | x |  | x | 11 | ON | L1 |  | ON | ON |  | L1+S2 |  | ON
 | STOP | 12 | x |  |  |  |  |  | x |  |  |  |  |  |  |  | x |  |  |  |  |  | x |  | x |  | 12 | H1 | L3
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

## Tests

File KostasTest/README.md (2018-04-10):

# KostasTest
<h1>AVR based Washing machine controller</h1>
<h2>Object</h2>
The prupose of this secondary software is to test the wiring of the relays.
The rotary encoder is used to select which relay is operated.
A short press on the switch will toggle the relay on / off.
A long press will reset all relays to off.

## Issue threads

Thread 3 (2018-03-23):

Relays association

emaschas, 2018-03-23:
Relays and their associated pins, shall be assigned to washing machine interface.
The related macros shall be created (by renaming _RELAYxx_ON_ and _RELAYxx_OFF_) .

costas233, 2018-03-23:
Relays :

Relay #1 Verrou porte
Com : 6E
NO : 5E (Verrou electrique)
NC : STOP light

Relay #2 Vanne froid
Com : Com Relay#3, #10 et #11 (hydrostat)
NO : 4E (electrovanne froid)
NC : -

Relay #3 vanne chaud
Com : Comme relay #2, #10 et #11 (hydrostat)
NO : 3D
NC : -

Relay #4 Chauffe
Com : 6E
NO : 12C (résistance chauffante)
NC : -

Relay #5 Vidange
Com : 6E
NO : 11C (pompe de vidange)
NC : -

Relay #6 Marche moteur
Com : 6E
NO : com relay #7 (Inversion moteur)
NC : -

Relay #7 Inversion moteur
Com : NO Relay #6
NO : 6D et com Relay #8 (vitesse lavage)
NC : 2E

Relay #8 Vitesse lavage ! couplé avec relay #9 (toujours dans le même état que relay #9)
Com : NO relay #6
NO : 2C (= moteur fil bleu/blanc, pin 3)
NC : 2D (= moteur fil rouge , pin 6)

Relay #9 Vitesse essorage ! couplé avec relay #8 (toujours dans le même état que relay #8)
Com : NO relay #6
NO : 6C (= moteur fil jaune, pin 2)
NC : 4D (= moteur fil bleu , pin 5)

! Avant de changer l'état des relais #7 #8 et #9 le moteur doit être arreté (relais #6 sur NC). Les deux relais #7 et #8 doivent changer d'état simultanément pour passe du mode vitesse lavage au mode vitesse essorage.

Relay #10 Niveau d'eau A. Ce relais fontionne à l'envers. (2 entrées une sortie)
Com : Com relay #2 et #3 (electrovannes)
NO : 8C Hydrostat A
NC : 7C Hydrostat A

Relay #11 Niveau d'eau B (extra wasser) Ce relais fontionne à l'envers. (2 entrées une sortie)
Com : Com relay #2 et #3 (electrovannes)
NO : 8C Hydrostat B
NC : 7C Hydrostat B

Relay #12 nc
Relay #13 nc
Relay #14 nc
Relay #15 nc
Relay #16 nc

costas233, 2018-03-23:
6E = phase 240V
9E, 10D, 12E, 11E, 11C, 10C = neutre 240V

costas233, 2018-03-23:
/////////////////////////////////////////////
// KostasWash v1.11                         //
// ---------------                         //
// Target CPU : Atmega8535 at 8MHz (int.)  //
/////////////////////////////////////////////

#include <avr/io.h>
#include <avr/interrupt.h>
#include <util/delay.h>
#include <stdio.h>
#include "TIMER.h"
#include "LCD.h"

//-----------------------------------------------------------------------------------
// WIRING
//-----------------------------------------------------------------------------------
// Human Interface
//-----------------------------------------------------------------------------------
// Encoder:
//   PD2 : Switch
//   PD3 : Clock
//   PD4 : Data
// LCD Display
//   PD7 : LCD_EN
//   PB0 : LCD_RS
//   PB3 : LCD_DB4
//   PB2 : LCD_DB5
//   PD6 : LCD_DB6
//   PD5 : LCD_DB7
//-----------------------------------------------------------------------------------
// Washing machine
//-----------------------------------------------------------------------------------
//   PA1 : Relay R01 Verrou porte Com : 6E NO : 5E (Verrou electrique) NC : STOP light
//   PA0 : Relay R02 Vanne froid Com : Com Relay#3#10#11 (hydrostat)NO : 4E (electrovanne froid) NC : -
//   PA3 : Relay R03 vanne chaud Com : Comme relay #2, #10 et #11 (hydrostat) NO : 3D NC : -
//   PA2 : Relay R04 Chauffe Com : 6EChauffe Com : 6E NO : 12C (résistance chauffante)
//   PA5 : Relay R05 Vidange Com : 6E NO : 11C (pompe de vidange)NC : -
//   PA4 : Relay R06 Marche moteur Com : 6E NO : com relay #7 (Inversion moteur)NC : -
//   PA7 : Relay R07 Inversion moteur Com : NO Relay #6 NO : 6D et com Relay #8 (vitesse lavage) NC : 2E
//   PA6 : Relay R08 Vitesse lavage Com : NO relay #6NO : 2C NC : 2D
//   PC7 : Relay R09 Vitesse essorage Com : NO relay #6 NO : 6C NC : 4D
//   PC3 : Relay R10 Niveau d'eau A Com : Com relay #2 et #3 (electrovannes)NO : 8C NC : 7C Hydrostat A
//   PC6 : Relay R11 Niveau d'eau B Com : Com relay #2 et #3 (electrovannes)NO : 8C NC : 7C Hydrostat B
//   PC2 : Relay R12 nc
//   PC5 : Relay R13 nc
//   PC1 : Relay R14 nc
//   PC4 : Relay R15 nc
//   PC0 : Relay R16 nc
//-----------------------------------------------------------------------------------

#define false   0
#define true  (!0)
#define off     0
#define on      1

// Shared Enumerations
// -------------------
enum SwitchStatus
{
  NO_PRESS,
  SHORT_PRESS,
  LONG_PRESS
};
enum MenuStatus
{
  WAIT_MENU,
  PROGRAM_MENU,
  DELAY_MENU,
  EXIT_MENU
};
enum WashStatus
{
  NO_WASH,
  PRE_WASH,
  MAIN_WASH,
  RINCE,
  DRY,
  END_WASH
};
enum RotationStatus
{
  NO_ROTATION,
  RUN1_ROTATION,
  PAUSE1_ROTATION,
  RUN2_ROTATION,
  PAUSE2_ROTATION
};

// Shared Variables
// ----------------
// System variables
volatile uint8_t  SwitchPressed  = NO_PRESS;
volatile uint8_t  EncoderChanged = false;
volatile uint8_t  EncoderCount   = 0;
// Program Variables : Menus
volatile uint8_t  MenuState = WAIT_MENU;
// Program Variables : Washing
volatile uint8_t  WashState = NO_WASH;
// Program Variables : Rotation (during Washing)
volatile uint8_t  RotationState = NO_ROTATION;

// Macros for Encoder
// ------------------
#define SWITCH     (PIND  &  _BV(PIND2))
#define ENCODER_A  (PIND  &  _BV(PIND3))
#define ENCODER_B  (PIND  &  _BV(PIND4))

// Macros for Relays
// ---------------
#define RELAY01_ON()  PORTA |=  _BV(PINA1)
#define RELAY01_OFF() PORTA &= ~_BV(PINA1)
#define RELAY02_ON()  PORTA |=  _BV(PINA0)
#define RELAY02_OFF() PORTA &= ~_BV(PINA0)
#define RELAY03_ON()  PORTA |=  _BV(PINA3)
#define RELAY03_OFF() PORTA &= ~_BV(PINA3)
#define RELAY04_ON()  PORTA |=  _BV(PINA2)
#define RELAY04_OFF() PORTA &= ~_BV(PINA2)
#define RELAY05_ON()  PORTA |=  _BV(PINA5)
#define RELAY05_OFF() PORTA &= ~_BV(PINA5)
#define RELAY06_ON()  PORTA |=  _BV(PINA4)
#define RELAY06_OFF() PORTA &= ~_BV(PINA4)
#define RELAY07_ON()  PORTA |=  _BV(PINA7)
#define RELAY07_OFF() PORTA &= ~_BV(PINA7)
#define RELAY08_ON()  PORTA |=  _BV(PINA6)
#define RELAY08_OFF() PORTA &= ~_BV(PINA6)
#define RELAY09_ON()  PORTC |=  _BV(PINC7)
#define RELAY09_OFF() PORTC &= ~_BV(PINC7)
#define RELAY10_ON()  PORTC |=  _BV(PINC3)
#define RELAY10_OFF() PORTC &= ~_BV(PINC3)
#define RELAY11_ON()  PORTC |=  _BV(PINC6)
#define RELAY11_OFF() PORTC &= ~_BV(PINC6)
#define RELAY12_ON()  PORTC |=  _BV(PINC2)
#define RELAY12_OFF() PORTC &= ~_BV(PINC2)
#define RELAY13_ON()  PORTC |=  _BV(PINC5)
#define RELAY13_OFF() PORTC &= ~_BV(PINC5)
#define RELAY14_ON()  PORTC |=  _BV(PINC1)
#define RELAY14_OFF() PORTC &= ~_BV(PINC1)
#define RELAY15_ON()  PORTC |=  _BV(PINC4)
#define RELAY15_OFF() PORTC &= ~_BV(PINC4)
#define RELAY16_ON()  PORTC |=  _BV(PINC0)
#define RELAY16_OFF() PORTC &= ~_BV(PINC0)

emaschas, 2018-03-25:
J'ai relu les affectations...
Est-ce qu'on a besoin de garder le montage en cascade de certains relais ?
On pourrait simplifier et retranscrire le fonctionnement en logiciel...

costas233, 2018-03-26:
J'étais malade ce we, Anatole m'a refile un rhume pas glop.  Les relais en cascade dont tu parles ce sont ceux du moteur ou des niveaux d'eau?

Pour le moteur, je ne penses pas qu'on puisse vraiment simplifier, ça marche comme ça :

phase ---- bobine stator 1 ----- bobine stator 2 ----- bobine rotor -----neutre
(avec un gros condensateur entre phase et neutre)
Pour changer de vitesse, on relie directement la bobine stator 1 à la bobine rotor (on change le nombre de bobinages)
Pour changer le sens de rotation on inverse la polarité au niveau de la bobine rotor.
Et avant de changer le sens ou la vitesse on coupe le circuit.
Il faut donc 2 relais.
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
costas233, 2018-04-10:
Proposition de modification de câblage :

Le thermostat est isolé de la résistance chauffante. On peut dont utiliser deux relais pour le mettre en série soi avec la résistance, soit avec l'électrovanne d'eau chaude

R05 com<---->t°<---->R07 com

Les bornes nc et no du relais R05 seraient reliées à C1 (niveau bas) et D11 (niveau ok)
Les bornes nc et no du relais R06 seraient reliées à D3 (vanne chaud) et C12 (chauffe)

Phase de remplissage R05 sur no et R06 sur no :

(niveau d'eau bas)----(thermostat)----(electrovanne chaud)

On remplis tant que la t° n'est pas atteinte, on n'ouvre pas encore la vanne froide.

Phase chauffe R05 sur nc et R06 sur nc :

(niveau d'eau ok)----(thermostat)---(chauffe)

On chauffe tant que la t° n'est pas atteinte, on ouvre la vanne froide pour compléter le niveau.

En résumé, on utilise le t° pour couper l'électrovanne chaude tant qu'on s'occupes de remplir la cuve.
Puis on utilise le t° pour couper la chauffe une fois que la cuve est pleine.

costas233, 2018-04-10:
En y réfléchissant c'est pas suffisant, on n'a pas la position neutre. il faudrait un 3e relais pour pouvoir couper à la fois la chauffe et l'admission d'eau chaude. Mais sur le paprier c'est possible. A étudier pour une version ultérieure.

emaschas, 2018-04-10:
Pas mal comme idée. Je vais y refléchir...
De toutes façons on a encore 5 relais disponibles...
Par contre on n'a pas de retour sur la température au niveau du micro-contrôleur.
Ou peut remplir en eau froide + eau chaude couplée au thermostat ce qui limite la température maximale, mais si l'eau est juste tiède on sera en dessous de la température souhaitée et il faudra compléter avec le chauffage.

costas233, 2018-04-10:
La séquence de remplissage / chauffe serait la suivante :

1) Remplissage uniquement en eau chaude, limité par le thermostat pendant qq minutes. Si l'eau est trop chaude, le remplissage s'arrête. Si l'eau est trop froide la cuve s'emplie et le 2) ne sert à rien.
2) Complément de remplissage froid sans limite + chaud limité par thermostat.
Si l'eau mitigée est trop chaude, l'admission d'eau chaude se fait par intermittence.
Si l'eau mitigée est trop froide, la chauffe sera complétée électriquement.
3) Chauffe électrique complémentaire limitée par thermostat.  Début du lavage.

Ca peut se chevaucher.

emaschas, 2018-04-17:
J'ai pas trouvé de solution sans prendre le risque de faire un court-circuit si les relais ne sont pas actionnés ensemble.
Il faut faire attention avec la resistance chauffante : 2000W ça fait 9A, les relais supportent juste 10A...

costas233, 2018-04-18:
La solution, je pense, c'est d'inclure un fusible en série avec la resistance. Dans le cas ou un des relais colle (ou en cas de bug du programme) c'est le fusible qui saute.
Si les 10A sont trop justes, il y a la possibilité de coupler deux relais en // et de les déclencher le plus simultanément possible. Ca réduira la possibilité de création d'un arc electrique au moment de la rupture et ça baissera l'effet Joules dans les relais. On a assez de relais pour ça.

Au passage, le même risque existe avec l'inversion moteur qui demande l'opération simultanée de deux relais. Et un fusible ne serait pas un luxe là aussi.

emaschas, 2018-04-19:
Pour avoir un câblage sans risques, il faudrait séparer les câbles des deux électrovannes du côté du connecteur D10 (câble bleu).
Peux-tu regarder si c'est faisable sans massacrer le câblage actuel ?

Sinon, pour l'inversion moteur, je ne vois pas où est le risque depuis qu'on a mis un relais pour le sens (R09) et un autre pour marche/arrêt (R08) ?
Les seuls relais qui doivent être synchrones sont R10 et R11 pour basculer la capacité entre lavage et essorage. S'ils ne sont pas synchrones on ne fait pas un court circuit on aura juste un moteur qui tourne mal ou pas du tout...

costas233, 2018-04-19:
C'est tres facile de recâbler les electrovannes, elles sont en haut, donc très accessibles. Il suffit de déconnecter les cosses de l'une d'elles et de tirer une nouvelle paire de câbles // au faiseau existant.
En fait c'est même sans doute plus facile que de passer par le connecteur 12 pins existant. Le seul souci est de ne pas inverser phase et neutre, et encore, je ne pense pas que ça pose un problème à la l'electrovanne.
Pour l'anecdote, j'ai appelé le magasin grec qui vendait le programmeur à 70€ : ça ne se fait plus. :-(
Sinon, j'ai trouvé des cosses standard sur l'ile. Y'a tout ce qu'il faut pour le cablage.

Closed 2018-05-06.

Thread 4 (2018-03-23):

Washing programs definitions

emaschas, 2018-03-23:
Create the real washing programs definitions in "_programs.h_".

costas233, 2018-03-23:
Relays :

Relay #1 Verrou porte
Com : 6E
NO : 5E (Verrou electrique)
NC : STOP light

Relay #2 Vanne froid
Com : Com Relay#3, #10 et #11 (hydrostat)
NO : 4E (electrovanne froid)
NC : -

Relay #3 vanne chaud
Com : Comme relay #z, #10 et #11 (hydrostat)
NO : 3D
NC : -

Relay #4 Chauffe
Com : 6E
NO : 12C (résistance chauffante)
NC : -

Relay #5 Vidange
Com : 6E
NO : 11C (pompe de vidange)
NC : -

Relay #6 Marche moteur
Com : 6E
NO : com relay #7 (Inversion moteur)
NC : -

Relay #7 Inversion moteur
Com : NO Relay #6
NO : 6D et com Relay #8 (vitesse lavage)
NC : 2E

Relay #8 Vitesse lavage ! couplé avec relay #9 (toujours dans le même état que relay #9)
Com : NO relay #6
NO : 2C (= moteur fil bleu/blanc, pin 3)
NC : 2D (= moteur fil rouge , pin 6)

Relay #9 Vitesse essorage ! couplé avec relay #8 (toujours dans le même état que relay #8)
Com : NO relay #6
NO : 6C (= moteur fil jaune, pin 2)
NC : 4D (= moteur fil bleu , pin 5)

! Avant de changer l'état des relais #7 #8 et #9 le moteur doit être arreté (relais #6 sur NC). Les deux relais #7 et #8 doivent changer d'état simultanément pour passe du mode vitesse lavage au mode vitesse essorage.

Relay #10 Niveau d'eau A. Ce relais fontionne à l'envers. (2 entrées une sortie)
Com : Com relay #2 et #3 (electrovannes)
NO : 8C Hydrostat A
NC : 7C Hydrostat A

Relay #11 Niveau d'eau B (extra wasser) Ce relais fontionne à l'envers. (2 entrées une sortie)
Com : Com relay #2 et #3 (electrovannes)
NO : 8C Hydrostat B
NC : 7C Hydrostat B

Relay #12 nc
Relay #13 nc
Relay #14 nc
Relay #15 nc
Relay #16 nc

costas233, 2018-03-23:
Pas mis dans le bon fil :-(

emaschas, 2018-04-10:
J'ai modifier le code pour mettre les programmes de lavage dans la mémoire "programme" (PROGMEM).
Résultat : on a 10% de mémoire "donnée" et 59.1% de la mémoire "programme" occupés.
Ce qui laisse de la place pour 478 lignes de programme de lavage (moins les textes si on en ajoute...).
Y a de quoi laver de plein de façons différentes !

emaschas, 2018-05-26:
Pour la suite fait un "Pull Request"...

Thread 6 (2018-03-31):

New wiring

emaschas, 2018-03-31:
The new wiring is proposed in the "documentation" folder : file "<a href="https://raw.githubusercontent.com/emaschas/KostasWash/matrix/Wiring_Power/NewWiring.png">NewWiring.png</a>" (the native files are in the Eagle_files directory).
11 relays are used...

emaschas, 2018-04-20:
<h1>Attention : </h1>
Maximum power = 2000 W (for the Heater)<br/>
=> Rating : 10 A<br/>
=> Cables : 1 mm2 minimum, 1.5 mm2 better

Closed 2018-05-06.

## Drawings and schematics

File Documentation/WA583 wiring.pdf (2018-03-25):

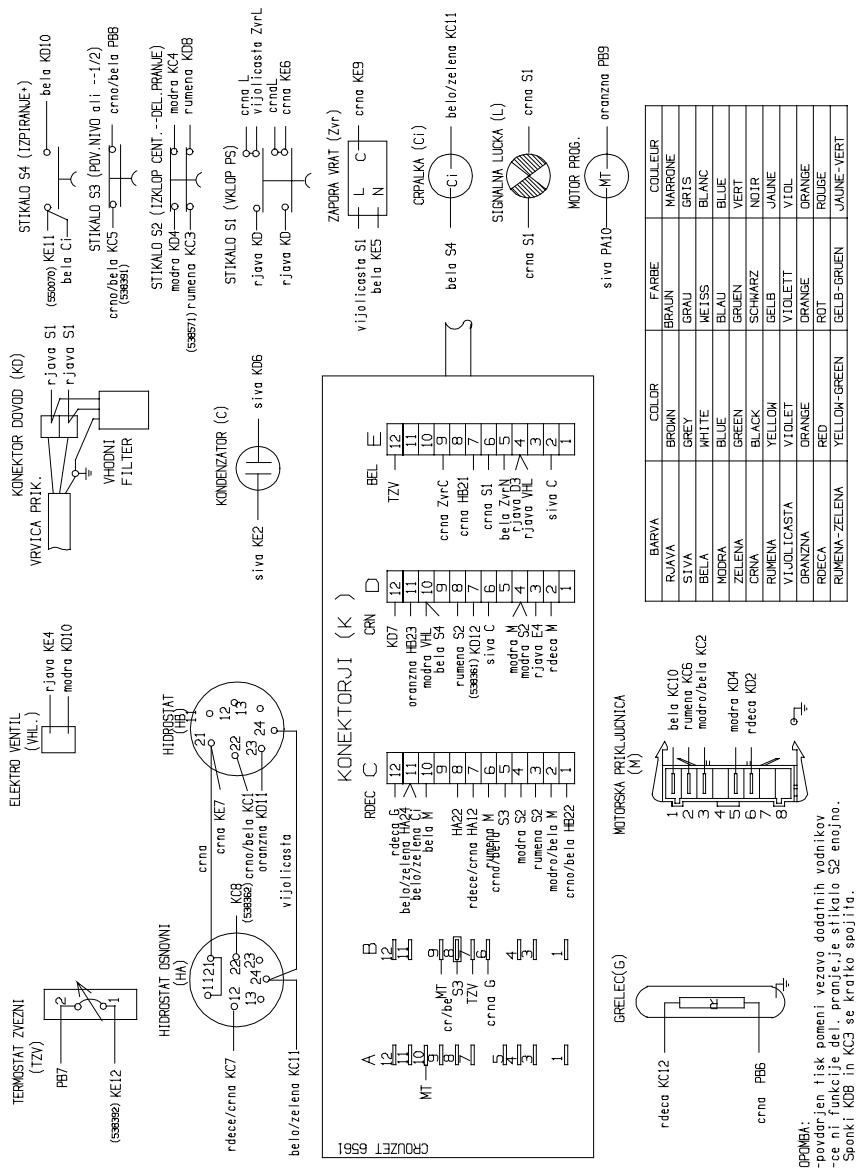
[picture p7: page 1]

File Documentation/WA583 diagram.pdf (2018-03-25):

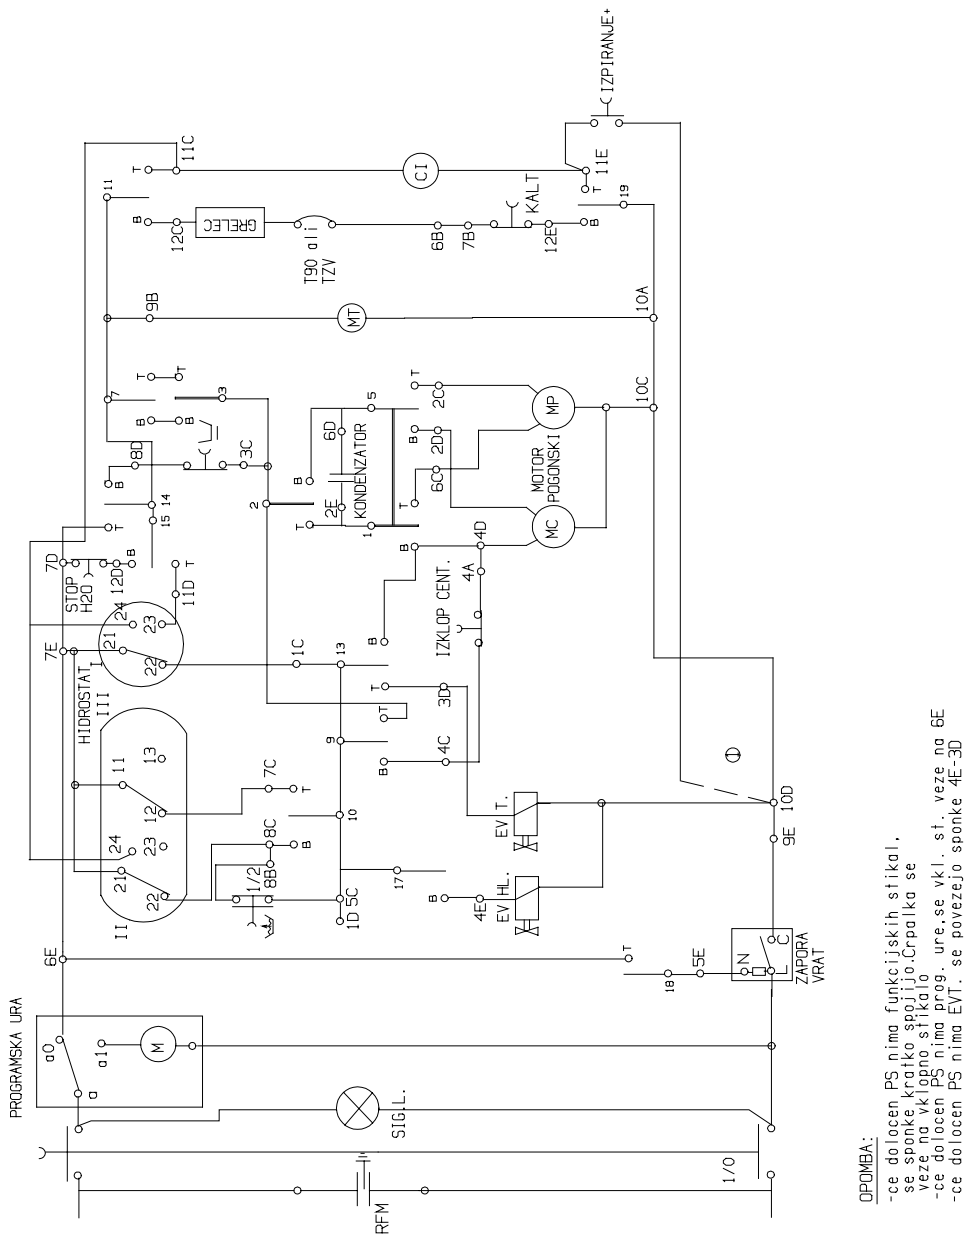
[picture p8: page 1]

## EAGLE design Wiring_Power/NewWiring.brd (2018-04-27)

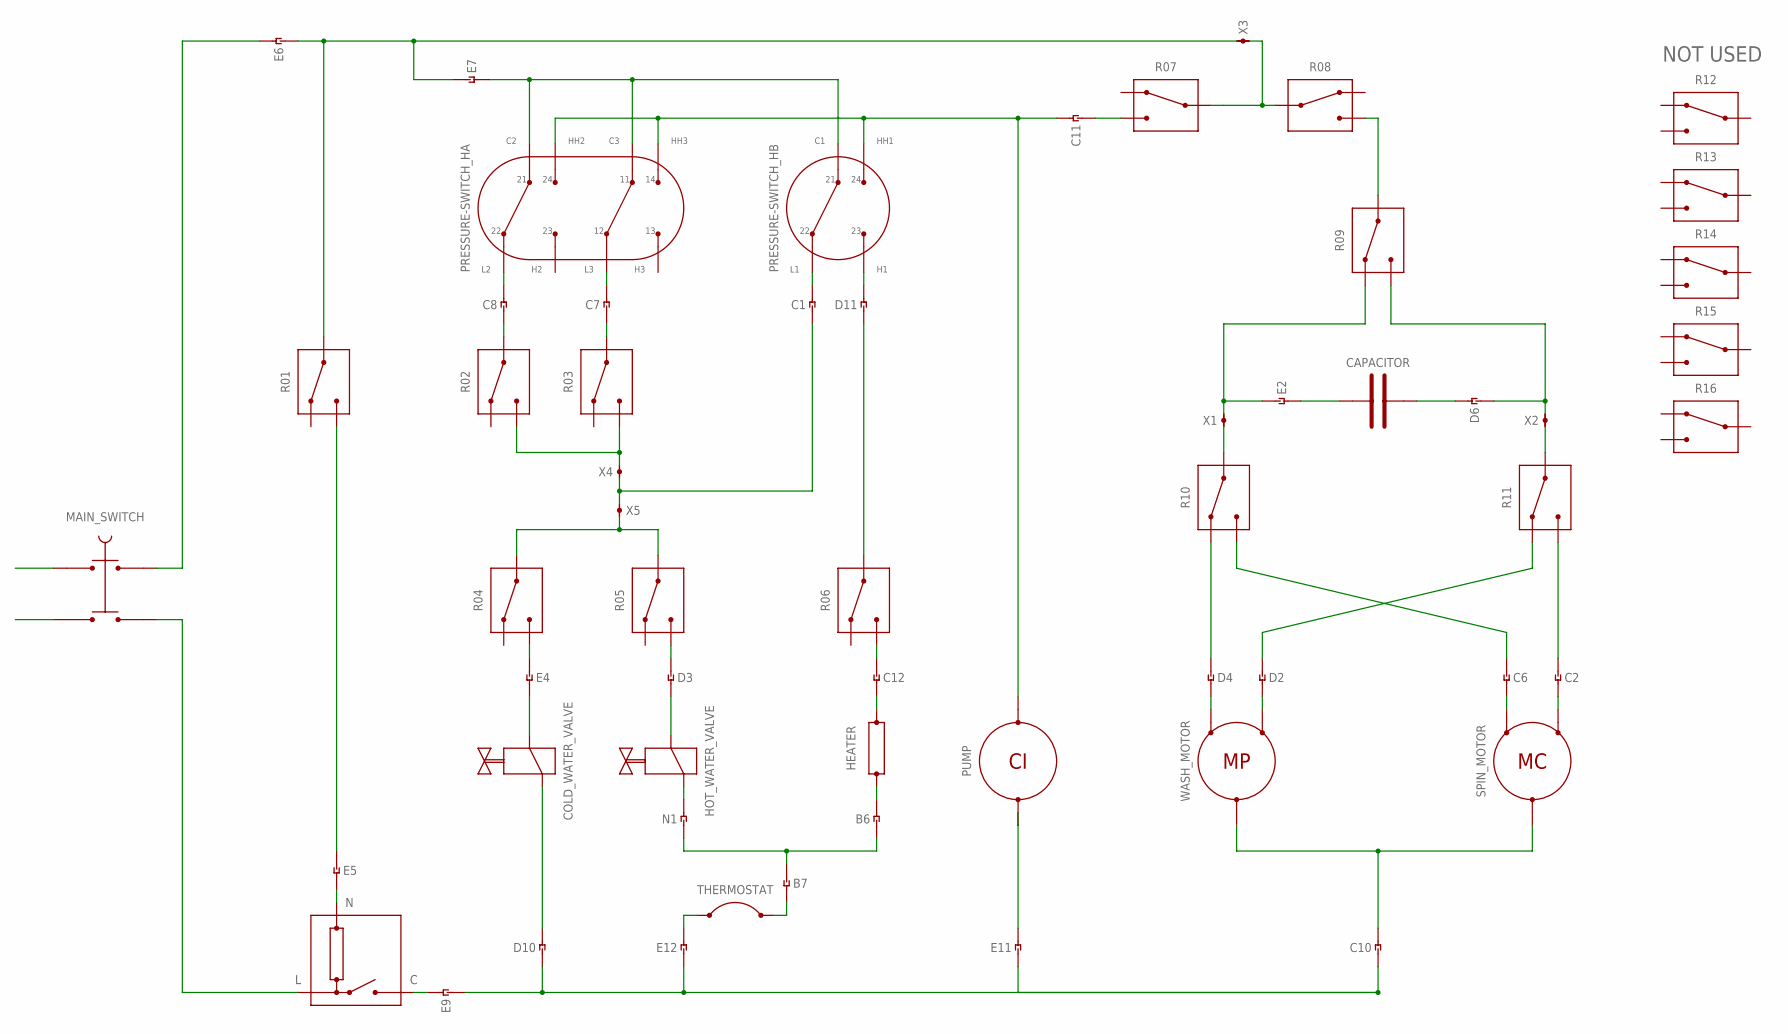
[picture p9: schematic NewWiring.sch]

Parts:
B6, B7: CABLE
C1, C2, C6, C7, C8, C10, C11, C12: CABLE
CAPACITOR: CAPACITOR
COLD_WATER_VALVE: VALVE
D2, D3, D4, D6, D10, D11: CABLE
E2, E4, E5, E6, E7, E9, E11, E12: CABLE
HEATER: HEATER
HOT_WATER_VALVE: VALVE
MAIN_SWITCH: SWITCH
N1: CABLE
PRESSURE-SWITCH_HA: PS2
PRESSURE-SWITCH_HB: PS1
PUMP: CI; MOTOR-2
R01, R02, R03, R04, R05, R06, R07, R08, R09, R10, R11, R12, R13, R14, R15, R16: RELAY
SPIN_MOTOR: MC; MOTOR-3
THERMOSTAT: THERMOSTAT
U$1: LOCK
WASH_MOTOR: MP; MOTOR-3
X1, X2, X3, X4, X5: DOMINO

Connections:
C1: C1.P$2 (PIN2), PRESSURE-SWITCH_HB.P$3
C10: C10.P$2 (PIN2), SPIN_MOTOR.MC, WASH_MOTOR.MC
C11-OVERFLOW: C11.P$2 (PIN2), PRESSURE-SWITCH_HA.P$5, PRESSURE-SWITCH_HA.P$8, PRESSURE-SWITCH_HB.P$2, PUMP.M1
D2: D2.P$2 (PIN2), WASH_MOTOR.M3 (M2)
D4: D4.P$2 (PIN2), WASH_MOTOR.M1
D6: CAPACITOR.C2, D6.P$2 (PIN2)
D10: COLD_WATER_VALVE.P$1, D10.P$2 (PIN2)
D11: D11.P$2 (PIN2), PRESSURE-SWITCH_HB.P$4
E5: E5.P$2 (PIN2), U$1.N
E11: E11.P$2 (PIN2), PUMP.M3 (M2)
LIVE: C10.P$1 (PIN1), D10.P$1 (PIN1), E9.P$1 (PIN1), E11.P$1 (PIN1), E12.P$1 (PIN1)
unnamed: E6.P$2 (PIN2), MAIN_SWITCH.O1 (OUT1)
unnamed: COLD_WATER_VALVE.P$2, E4.P$2 (PIN2)
unnamed: MAIN_SWITCH.O2 (OUT2), U$1.L
unnamed: D3.P$2 (PIN2), HOT_WATER_VALVE.P$2
unnamed: B6.P$1 (PIN1), B7.P$1 (PIN1), N1.P$1 (PIN1)
unnamed: E5.P$1 (PIN1), R01.T
unnamed: D4.P$1 (PIN1), R10.R
unnamed: C2.P$1 (PIN1), R11.T
unnamed: C6.P$1 (PIN1), R10.T
unnamed: R08.T, R09.C
unnamed: HOT_WATER_VALVE.P$1, N1.P$2 (PIN2)
unnamed: D2.P$1 (PIN1), R11.R
unnamed: R10.C, X1.P$1 (PIN1)
unnamed: R02.T, R03.T, X4.P$2 (PIN2)
unnamed: C8.P$2 (PIN2), PRESSURE-SWITCH_HA.P$2
unnamed: C7.P$2 (PIN2), PRESSURE-SWITCH_HA.P$6
unnamed: C6.P$2 (PIN2), SPIN_MOTOR.M1
unnamed: E9.P$2 (PIN2), U$1.C
unnamed: C12.P$2 (PIN2), HEATER.H2
unnamed: E12.P$2 (PIN2), THERMOSTAT.T2
unnamed: C12.P$1 (PIN1), R06.T
unnamed: C11.P$1 (PIN1), R07.T
unnamed: D3.P$1 (PIN1), R05.T
unnamed: C2.P$2 (PIN2), SPIN_MOTOR.M3 (M2)
unnamed: E2.P$1 (PIN1), R09.R, X1.P$2 (PIN2)
unnamed: B7.P$2 (PIN2), THERMOSTAT.T1
unnamed: B6.P$2 (PIN2), HEATER.H1
unnamed: D6.P$1 (PIN1), R09.T, X2.P$2 (PIN2)
unnamed: R11.C, X2.P$1 (PIN1)
unnamed: R07.C, R08.C, X3.P$2 (PIN2)
unnamed: CAPACITOR.C1, E2.P$2 (PIN2)
unnamed: R04.C, R05.C, X5.P$2 (PIN2)
unnamed: E7.P$2 (PIN2), PRESSURE-SWITCH_HA.P$1, PRESSURE-SWITCH_HA.P$4, PRESSURE-SWITCH_HB.P$1
unnamed: C8.P$1 (PIN1), R02.C
unnamed: C7.P$1 (PIN1), R03.C
unnamed: D11.P$1 (PIN1), R06.C
unnamed: E4.P$1 (PIN1), R04.T
NEUTRAL: E6.P$1 (PIN1), E7.P$1 (PIN1), R01.C, X3.P$1 (PIN1)
PHASE3: C1.P$1 (PIN1), X4.P$1 (PIN1), X5.P$1 (PIN1)

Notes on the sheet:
NOT USED

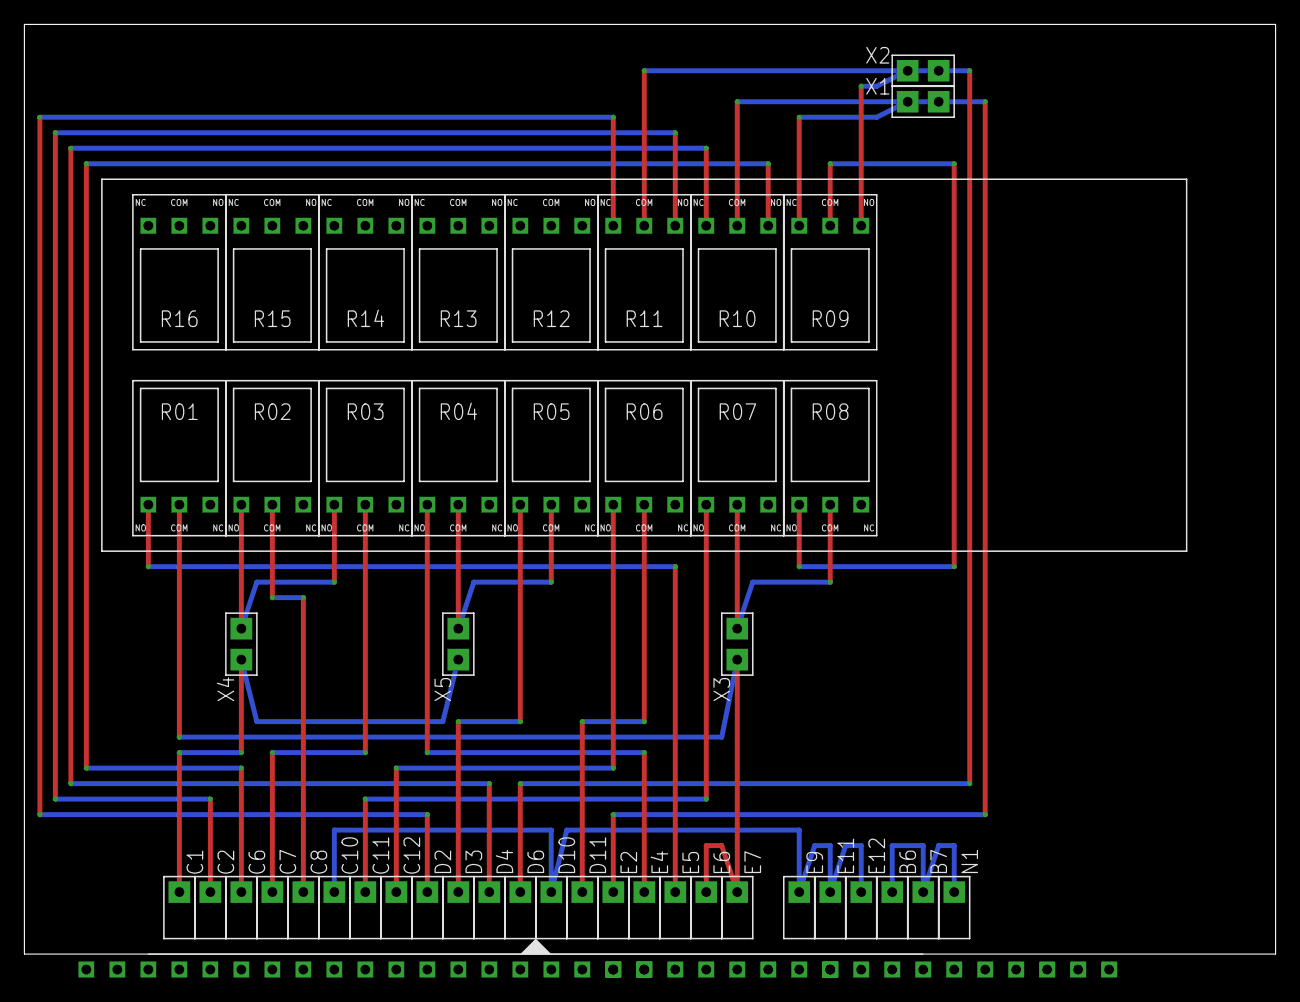
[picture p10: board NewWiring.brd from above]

Board: 2 copper layers, 102.5 x 76.2 mm, 58 parts (0 on the bottom side), 50 nets.

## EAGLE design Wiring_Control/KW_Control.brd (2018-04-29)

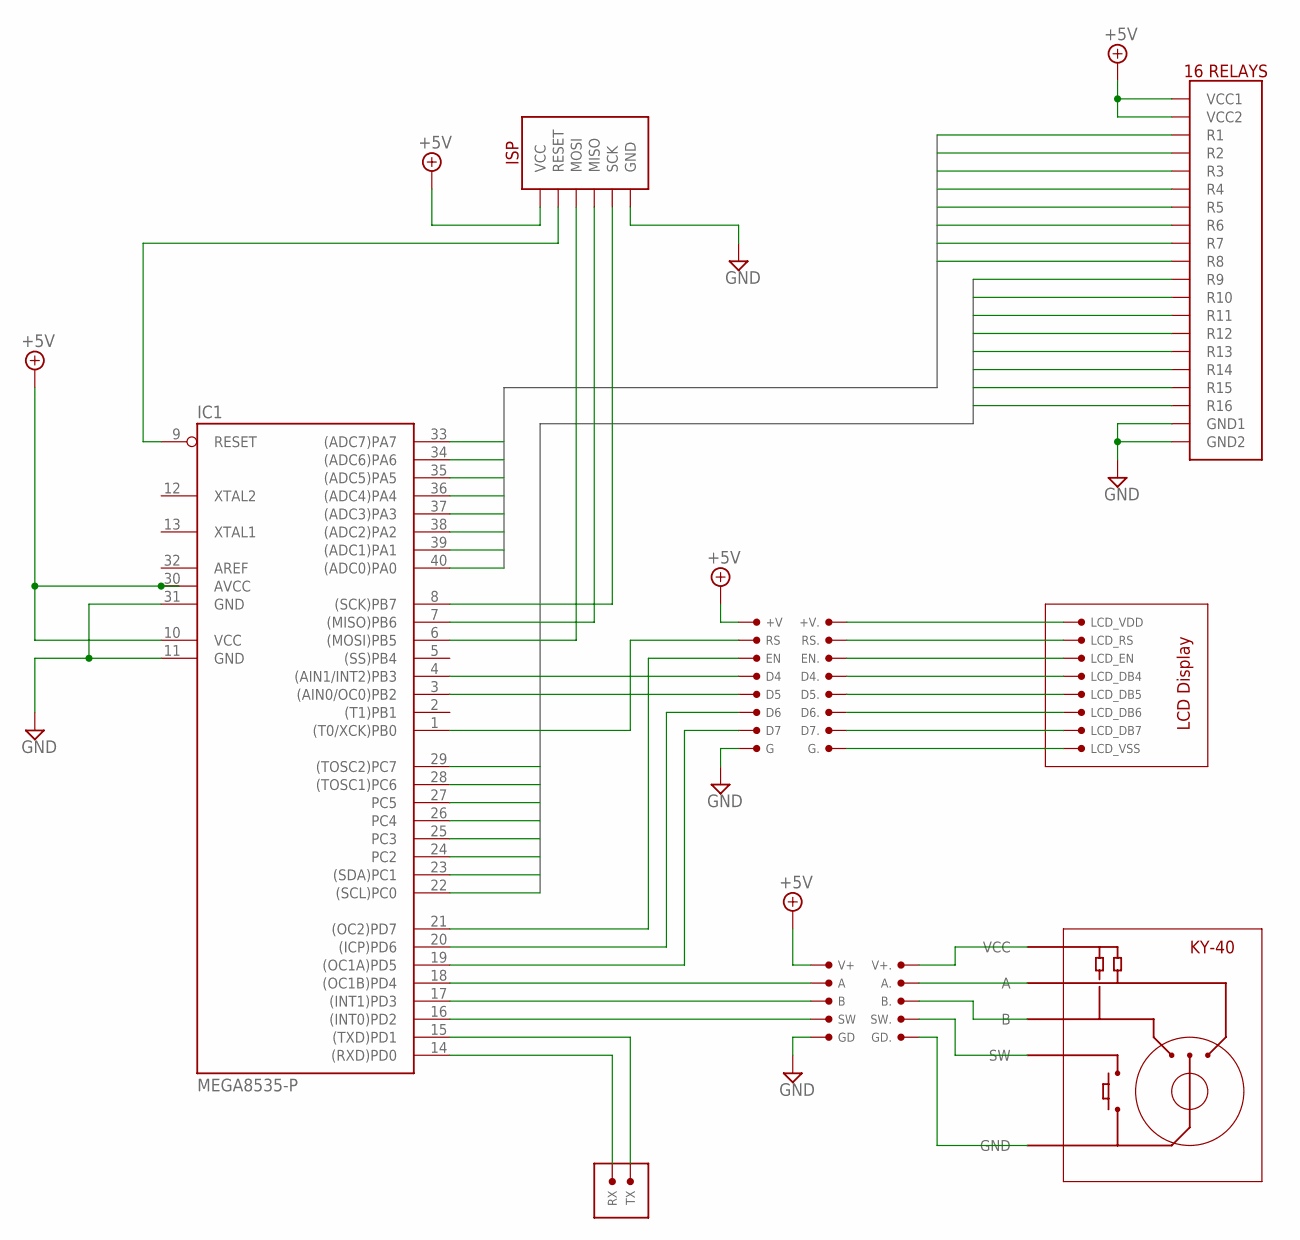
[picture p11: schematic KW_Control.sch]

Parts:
+V, +V.: PIN
A, A.: PIN
B, B.: PIN
D4, D4., D5, D5., D6, D6., D7, D7.: PIN
EN, EN.: PIN
G, G.: PIN
GD, GD.: PIN
IC1: MEGA8535-P; DIL40
IC2: KY-40
LCD_DB4, LCD_DB5, LCD_DB6, LCD_DB7: PIN
LCD_EN: PIN
LCD_RS: PIN
LCD_VDD: PIN
LCD_VSS: PIN
RS, RS.: PIN
RX: PIN
SW, SW.: PIN
TX: PIN
U$1: ISP
U$2: RELAYS-16
V+, V+.: PIN

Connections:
+5V: +V.P$1, IC1.10 (VCC), IC1.30 (AVCC), U$1.VCC, U$2.VCC1, U$2.VCC2, V+.P$1
A1: IC1.40 ((ADC0)PA0), U$2.1 (R1)
A2: IC1.39 ((ADC1)PA1), U$2.2 (R2)
A3: IC1.38 ((ADC2)PA2), U$2.3 (R3)
A4: IC1.37 ((ADC3)PA3), U$2.4 (R4)
A5: IC1.36 ((ADC4)PA4), U$2.5 (R5)
A6: IC1.35 ((ADC5)PA5), U$2.6 (R6)
A7: IC1.34 ((ADC6)PA6), U$2.7 (R7)
A8: IC1.33 ((ADC7)PA7), U$2.8 (R8)
B1: IC1.22 ((SCL)PC0), U$2.9 (R9)
B2: IC1.23 ((SDA)PC1), U$2.10 (R10)
B3: IC1.24 (PC2), U$2.11 (R11)
B4: IC1.25 (PC3), U$2.12 (R12)
B5: IC1.26 (PC4), U$2.13 (R13)
B6: IC1.27 (PC5), U$2.14 (R14)
B7: IC1.28 ((TOSC1)PC6), U$2.15 (R15)
B8: IC1.29 ((TOSC2)PC7), U$2.16 (R16)
GND: G.P$1, GD.P$1, IC1.11 (GND), IC1.31 (GND), U$1.GND, U$2.GND1, U$2.GND2
MISO: IC1.7 ((MISO)PB6), U$1.MISO
MOSI: IC1.6 ((MOSI)PB5), U$1.MOSI
unnamed: D7.P$1, IC1.19 ((OC1A)PD5)
unnamed: D6.P$1, IC1.20 ((ICP)PD6)
unnamed: D5.P$1, IC1.3 ((AIN0/OC0)PB2)
unnamed: D4.P$1, IC1.4 ((AIN1/INT2)PB3)
unnamed: +V..P$1, LCD_VDD.P$1
unnamed: G..P$1, LCD_VSS.P$1
unnamed: D4..P$1, LCD_DB4.P$1
unnamed: D7..P$1, LCD_DB7.P$1
unnamed: A.P$1, IC1.18 ((OC1B)PD4)
unnamed: B.P$1, IC1.17 ((INT1)PD3)
unnamed: IC1.16 ((INT0)PD2), SW.P$1
unnamed: A..P$1, IC2.A
unnamed: B..P$1, IC2.B
unnamed: IC2.SW, SW..P$1
unnamed: IC2.VCC, V+..P$1
unnamed: GD..P$1, IC2.GND
unnamed: D6..P$1, LCD_DB6.P$1
unnamed: EN..P$1, LCD_EN.P$1
unnamed: LCD_RS.P$1, RS..P$1
unnamed: D5..P$1, LCD_DB5.P$1
unnamed: EN.P$1, IC1.21 ((OC2)PD7)
unnamed: IC1.1 ((T0/XCK)PB0), RS.P$1
RESET: IC1.9 (RESET), U$1.RESET
RX: IC1.14 ((RXD)PD0), RX.P$1
SCK: IC1.8 ((SCK)PB7), U$1.SCK
TX: IC1.15 ((TXD)PD1), TX.P$1

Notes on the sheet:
LCD Display

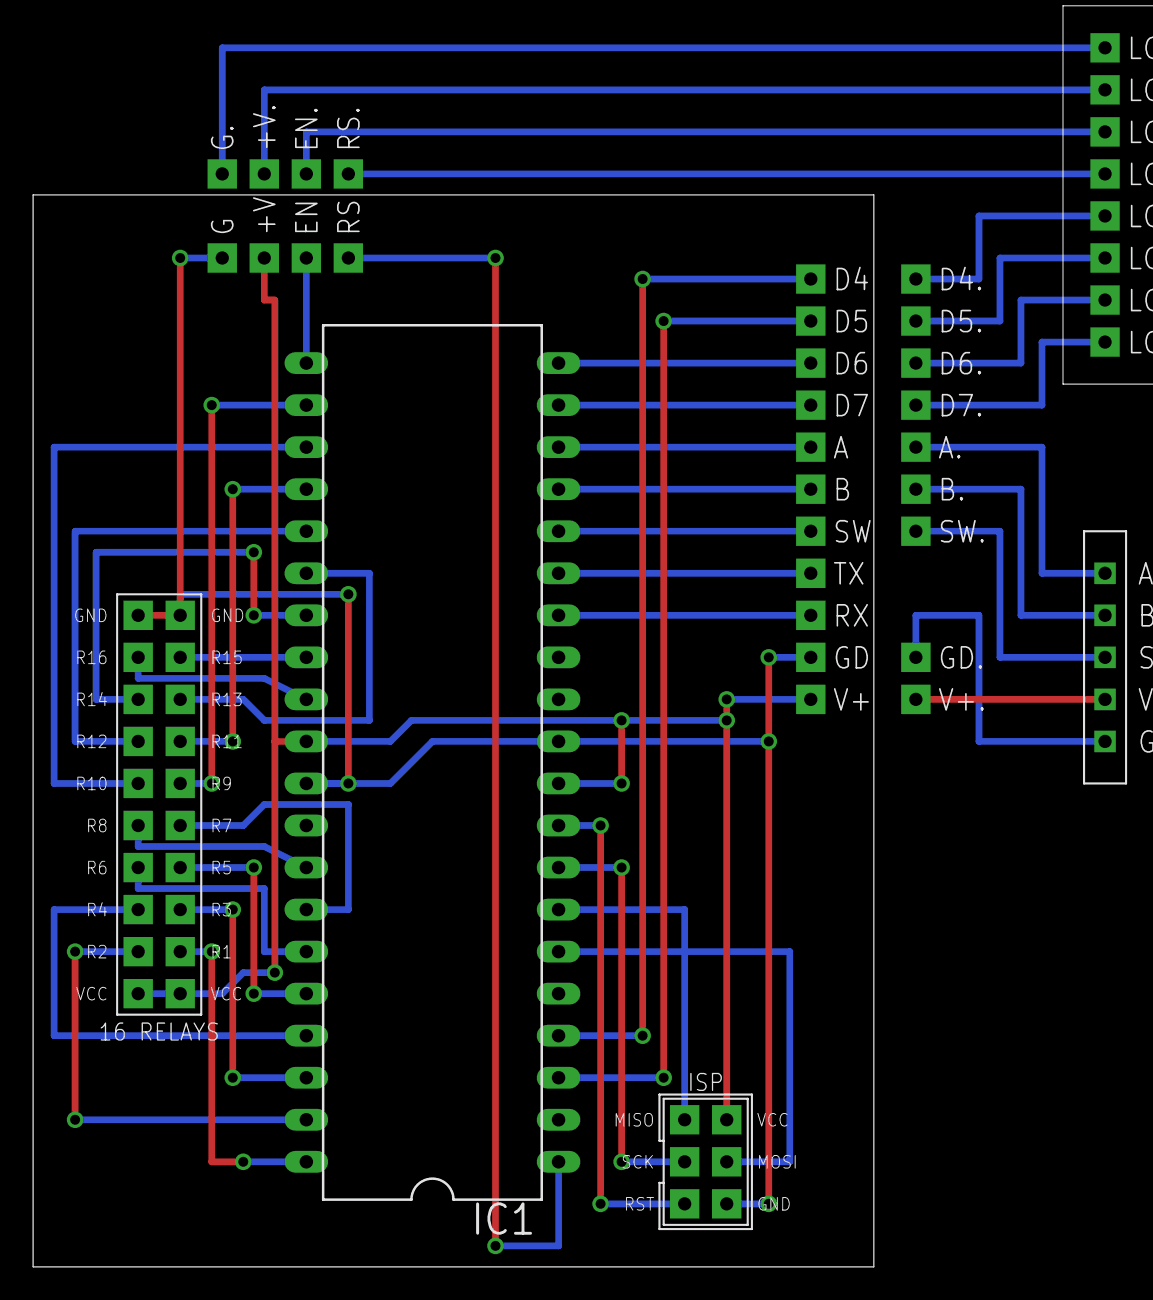
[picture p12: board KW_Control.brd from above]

Board: 2 copper layers, 50.8 x 64.8 mm, 40 parts (0 on the bottom side), 46 nets.

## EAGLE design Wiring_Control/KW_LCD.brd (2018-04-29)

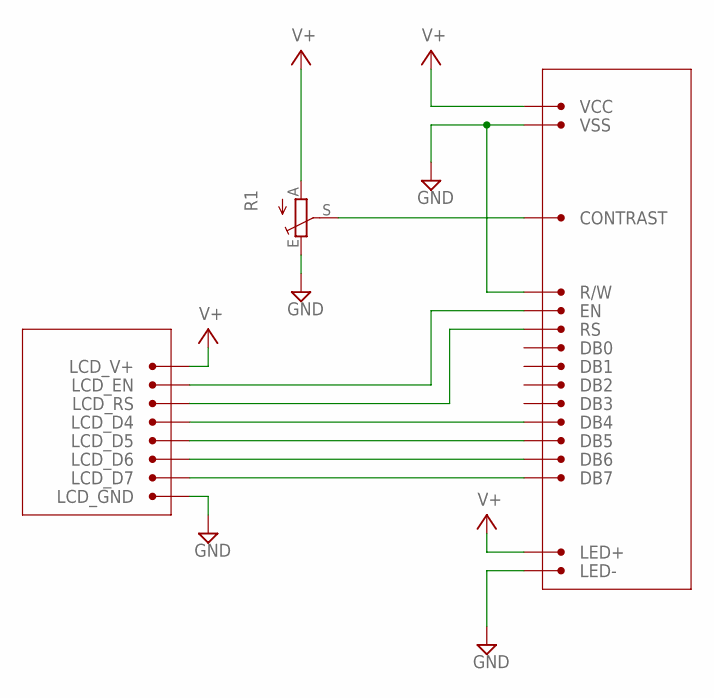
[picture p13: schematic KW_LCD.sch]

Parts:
CONTRAST: 3; CONN
DB0: 7; CONN
DB1: 8; CONN
DB2: 9; CONN
DB3: 10; CONN
DB4: 11; CONN
DB5: 12; CONN
DB6: 13; CONN
DB7: 14; CONN
EN: 6; CONN
LCD_D4, LCD_D5, LCD_D6, LCD_D7: 14; CONN
LCD_EN: 14; CONN
LCD_GND: 14; CONN
LCD_RS: 14; CONN
LCD_V+: 14; CONN
LED+: 16; CONN
LED-: 15; CONN
R1: TRIM_EU-ECP10S; ECP10S
R/W: 5; CONN
RS: 4; CONN
VCC: 2; CONN
VSS: 1; CONN

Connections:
GND: LCD_GND.P$1, LED-.P$1, R1.E, R/W.P$1, VSS.P$1
unnamed: DB7.P$1, LCD_D7.P$1
unnamed: DB6.P$1, LCD_D6.P$1
unnamed: LCD_RS.P$1, RS.P$1
unnamed: CONTRAST.P$1, R1.S
unnamed: EN.P$1, LCD_EN.P$1
unnamed: DB5.P$1, LCD_D5.P$1
unnamed: DB4.P$1, LCD_D4.P$1
V+: LCD_V+.P$1, LED+.P$1, R1.A, VCC.P$1

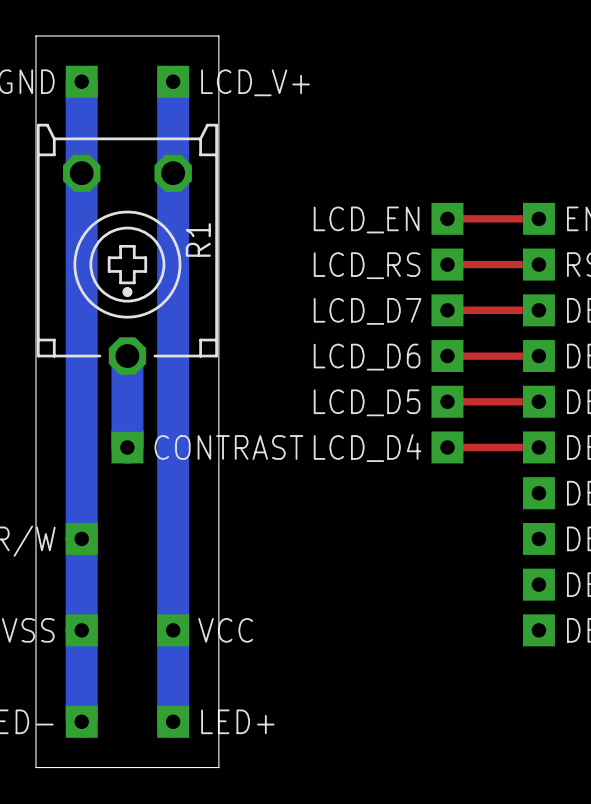
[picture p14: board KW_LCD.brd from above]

Board: 2 copper layers, 10.2 x 40.6 mm, 25 parts (0 on the bottom side), 9 nets.

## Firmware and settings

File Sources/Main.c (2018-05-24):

/////////////////////////////////////////////
// KostasWash v3.5                         //
// ---------------                         //
// Target CPU : Atmega8535 at 8MHz (int.)  //
/////////////////////////////////////////////

#include "Hardware.h"
#include "Washing.h"
#include <avr/pgmspace.h>

// System variables
volatile uint8_t  SwitchPressed  = NO_PRESS;
volatile uint8_t  EncoderChanged = false;
volatile uint8_t  EncoderCount   = 0;

//-----------------------------------------------------------------------------------
// Interrupt Service Routine : Pin change for Switch (INT0=PD2)
//-----------------------------------------------------------------------------------
ISR(INT0_vect)
{
  #define LONG_PRESS_TIME 1000 // milliseconds
  if(CountDown3 < (LONG_PRESS_TIME-20)) // Debouce time 20ms
  {
    if(SWITCH) // On=Released
      SwitchPressed = (CountDown3 == 0 ? LONG_PRESS : SHORT_PRESS);
    else // Off=Pressed
      CountDown3 = LONG_PRESS_TIME;
  }
}

//-----------------------------------------------------------------------------------
// Interrupt Service Routine : Pin change for Encoder A (INT1=PD3)
//-----------------------------------------------------------------------------------
ISR(INT1_vect)
{
  if(CountDown4 == 0)
  {
    if(ENCODER_B) EncoderCount--; else EncoderCount++;
    EncoderChanged = true;
    CountDown4 = 60; // Debouce time 60ms
  }
}

//-----------------------------------------------------------------------------------
// Initialisation
//-----------------------------------------------------------------------------------
void initialise(void)
{
  // Ports direction
  DDRA = 0xFF;                           // PORTA Output for Relays
  DDRC = 0xFF;                           // PORTC Output for Relays  
  DDRB = _BV(PB0) | _BV(PB2) | _BV(PB3); // PB0, PB2 and PB3 Output for LCD
  DDRD = _BV(PD5) | _BV(PD6) | _BV(PD7); // PD5, PD6 and PD7 Output for LCD
  // All relays to 1 (inverted logic)
  PORTA = 0xFF;
  PORTC = 0xFF;
  // Pull up resitors
  PORTD = _BV(PD2) | _BV(PD3) | _BV(PD4);// Pin D2,D3,D4 Pull Up for Switch and encoder
  // Define interrupt on pin change (INT0=PD2 and INT1=PD3)
  MCUCR = _BV(ISC11) | _BV(ISC00);       // ISC1=10 Interrupt on falling edge, ISC0=01 on any change
  GICR  = _BV(INT0)  | _BV(INT1);        // Enable INT0 and INT1 interrupts
  sei();                                 // Enable Interrupts
  // Start Timer
  initTimer();
  // LCD
  LCD_begin();
  LCD_specialCar();
  LCD_puts_P(PSTR("KostasWash v3.5\n"));
  _delay_ms(1000);
  LCD_cls();
  DisplayProgram();
}


//-----------------------------------------------------------------------------------
// MAIN
//-----------------------------------------------------------------------------------
int main(void)
{
  initialise();
  SwitchPressed  = NO_PRESS;
  EncoderChanged = false;
  //
  // Main loop
  // ---------
  while(1)
  {
    // Check is the encoder's switch has changed
    // -----------------------------------------
    if(SwitchPressed)
    {
      if(SwitchPressed == SHORT_PRESS)
      {
        if(NoWash()) StartWash(); 
        else AbortWash();
      }
      else // LONG_PRESS = Emergency Stop...
      {
        PORTA = 0xFF; // Stop everything : All relays to 1 (inverted logic)
        PORTC = 0xFF;        
        LCD_cls();
        LCD_puts_P(PSTR("Emergency STOP\n"));
        _delay_ms(3000);
        DisplayProgram();
        // while(!0); // Loop for ever
        // RESET to restart !
      }
      SwitchPressed = NO_PRESS;
    }
    // Check if the encoder counter has changed
    // ----------------------------------------
    if(EncoderChanged)
    {
      if( NoWash() ) SelectProgram(EncoderCount);
      EncoderChanged = false;
    }
    // Update Rotation Machine State
    // -------------------------------
    RotationControl();
    // Update Washing Machine State
    // ------------------------------
    WashControl();
  }
  // End of the Main loop (never ends)
  // ---------------------------------
}

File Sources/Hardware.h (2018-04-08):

/////////////////////////////////////////////
// KostasWash v1.1                         //
// ---------------                         //
// Target CPU : Atmega8535 at 8MHz (int.)  //
/////////////////////////////////////////////

#include <avr/io.h>
#include <avr/interrupt.h>
#include <util/delay.h>
#include <stdio.h>
#include "TIMER.h"
#include "LCD.h"

//-----------------------------------------------------------------------------------
// WIRING
//-----------------------------------------------------------------------------------
// Human Interface
//-----------------------------------------------------------------------------------
// Encoder:
//   PD2 : Switch 
//   PD3 : Clock
//   PD4 : Data
// LCD Display
//   PD7 : LCD_EN
//   PB0 : LCD_RS
//   PB3 : LCD_DB4
//   PB2 : LCD_DB5
//   PD6 : LCD_DB6
//   PD5 : LCD_DB7
//-----------------------------------------------------------------------------------
// Washing machine 
//-----------------------------------------------------------------------------------------------------------------------------
// PA1 : Relay R01 Verrou porte      COM : (6E)                        NO : (5E) Verrou electrique        NC : (??) STOP light
// PA0 : Relay R02 Vanne froid       COM : COM.R03+R10+R11 Hydrostat   NO : (4E) Electrovanne froid       NC : -
// PA3 : Relay R03 vanne chaud       COM : COM.R02+R10+R11 Hydrostat   NO : (3D)                          NC : -
// PA2 : Relay R04 Chauffe           COM : (6E)                        NO : (12C) Résistance chauffante   NC : -
// PA5 : Relay R05 Vidange           COM : (6E)                        NO : (11C) Pompe de vidange        NC : -
// PA4 : Relay R06 Marche moteur     COM : (6E)                        NO : COM.R07 Inversion moteur      NC : -
// PA7 : Relay R07 Inversion moteur  COM : NO.R06                      NO : (6D) + COM.R08 Vitesse lavage NC : (2E)
// PA6 : Relay R08 Vitesse lavage    COM : NO.R06                      NO : (2C)                          NC : (2D)
// PC7 : Relay R09 Vitesse essorage  COM : NO.R06                      NO : (6C)                          NC : (4D)
// PC3 : Relay R10 Niveau d'eau A    COM : COM.R02+R03 Electrovannes   NO : (8C)                          NC : (7C) Hydrostat A
// PC6 : Relay R11 Niveau d'eau B    COM : COM.R02+R03 Electrovannes   NO : (8C)                          NC : (7C) Hydrostat B
// PC2 : Relay R12 nc
// PC5 : Relay R13 nc
// PC1 : Relay R14 nc
// PC4 : Relay R15 nc
// PC0 : Relay R16 nc
//-----------------------------------------------------------------------------------------------------------------------------

#define false   0
#define true  (!0)
#define off     0
#define on      1

// Shared Enumerations
// -------------------
enum SwitchStatus 
{ 
  NO_PRESS,
  SHORT_PRESS,
  LONG_PRESS
};

// Macros for Encoder
// ------------------
#define SWITCH     (PIND  &  _BV(PIND2))
#define ENCODER_A  (PIND  &  _BV(PIND3))
#define ENCODER_B  (PIND  &  _BV(PIND4))

// Masks definition for "step"
// ---------------------------
// PORTA : MSB - PORTC : LSB
#define LOCK   (_BV(1))            // R01 - PINA1 - DOOR LOCK
#define LEV1   0                   // Level 1 is always available
#define LEV2   (_BV(0))            // R02 - PINA0 - WATER LEVEL 2
#define LEV3   (_BV(3))            // R03 - PINA3 - WATER LEVEL 3
#define EVCOLD (_BV(2))            // R04 - PINA2 - ELECTROVALVE COLD WATER
#define EVHOT  (_BV(5))            // R05 - PINA5 - ELECTROVALVE HOT WATER
#define HEAT   (_BV(4))            // R06 - PINA4 - HEATER ON
#define DRAIN  (_BV(7))            // R07 - PINA7 - DRAIN PUMP
#define MOTOR  (_BV(6))            // R08 - PINA6 - WASH/SPIN MOTOR ON
#define REV    (_BV(7+8))          // R09 - PINC7 - REVERSE MOTOR DIRECTION
#define SPIN   (_BV(3+8)|_BV(6+8)) // R10+R11 - PINC3+PINC6 - SPIN SPEED (ELSE WASH SPEED)
#define R12    (_BV(2+8))          // R12 - PINC2 - NOT USED
#define R13    (_BV(5+8))          // R13 - PINC5 - NOT USED
#define R14    (_BV(1+8))          // R14 - PINC1 - NOT USED
#define R15    (_BV(4+8))          // R15 - PINC4 - NOT USED
#define R16    (_BV(0+8))          // R16 - PINC0 - NOT USED

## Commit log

2018-03-13 Filter on dirs
2018-03-16 Added relay masks
2018-03-19 Corrected display at start
    [Washing.c]
2018-03-20 Added parameter for long switch press time
2018-03-24 Updated relay description
2018-03-25 Added WA583 wiring
2018-03-27 Added 6561 sequences
    [CROUZET 6561 Sequences.xlsx]
2018-03-27 Updated sequence
    [CROUZET 6561 Sequences.xlsx]
2018-03-27 Added New Schematic
    [NewWiring.sch]
2018-03-30 Added simulator
    [CROUZET 6561 Sequences.xlsx]
2018-03-31 New Wiring
    [NewWiring.sch]
2018-04-08 Modified wiring of R08 and R09
    [NewWiring.sch]
2018-04-09 Updated documentation
    [CROUZET 6561 Sequences.xlsx]
2018-04-09 Added KostasTest for wiring checking
2018-04-13 Added connectors
    [Connectors.xlsx, NewWiring.sch]
2018-04-24 Added Cabling
    [NewWiring.brd, NewWiring.sch]
2018-04-29 Added Control Wiring
    [KW_Control.brd, KW_Control.sch, KW_LCD.brd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]
2025-05-03 Elecric motor plate
